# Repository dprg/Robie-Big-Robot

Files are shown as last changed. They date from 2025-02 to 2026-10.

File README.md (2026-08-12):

# Robie-Big-Robot
Files related to Robie, the 7-foot tall DPRG mascot.

# Repo Contents

CAD models are in [mechanical/cad_files](mechanical/cad_files) . At the time of repo creation they contained 
the design files delivered by Ron Grant to Paul Bouchier on 26 Feb 2025.

Arduino files are as delivered by Doug Paradis to Paul Bouchier on March 2 2025. 
Mike Williamson added the Robie_neck_eyes code for the head UNO 7/7/2026.

Raspberry Pi4 files TBD
=======

There are two Arduino source code directories:

1. `Big_robot_pgm1` contains arduino code for the body and arm motors, which are controlled by
the arduino mega in the torso.
2. `Robie_neck_eyes` contains arduino code for the head motors and eye LEDs.

# Raspberry Pi Head Tracking

1. Connect to Robie's AP: `robiewifi`, wifi passwd is inside the body
2. You will get an IP at: `10.42.0.x`
3. ssh into the RPi: `ssh robie@10.42.0.1` # passwd is inside the body
4. Use aliases `miniterm_head` and `miniterm_body` to connect to the arduinos and manually issue commands. `Ctrl-]` to exit
5. Connect a NoMachine client to robie desktop as above
6. launch a terminal session on the desktop
7. In the terminal session:
   - `cd Robie-Big-Robot/src`
   - `source venv/bin/activate`
   - `python face_detector.py`

# Motors

### New Head Pan Motor

A stepper motor to pan the head is now located in the neck of Robie instead of in the torso.

The head motor is a NEMA 11 motor from stepperonline.com, P/N 11HS20-0674S.
[Specs here](https://www.omc-stepperonline.com/nema-11-bipolar-1-8deg-12ncm-17oz-in-0-67a-6-2v-28x28x51mm-4-wires-11hs20-0674s)

There are still 20 command steps for full range using 'L' and 'R' char commands.
There is also a new head center 'C' command.

### New Head Tilt Motor

The head tilt motor is a NEMA 17 motor from stepperonline.com, P/N 17HS19-2004S1.

#### Specs
[Full size image](images/NEMA17-Motor-spec.webp)<br>
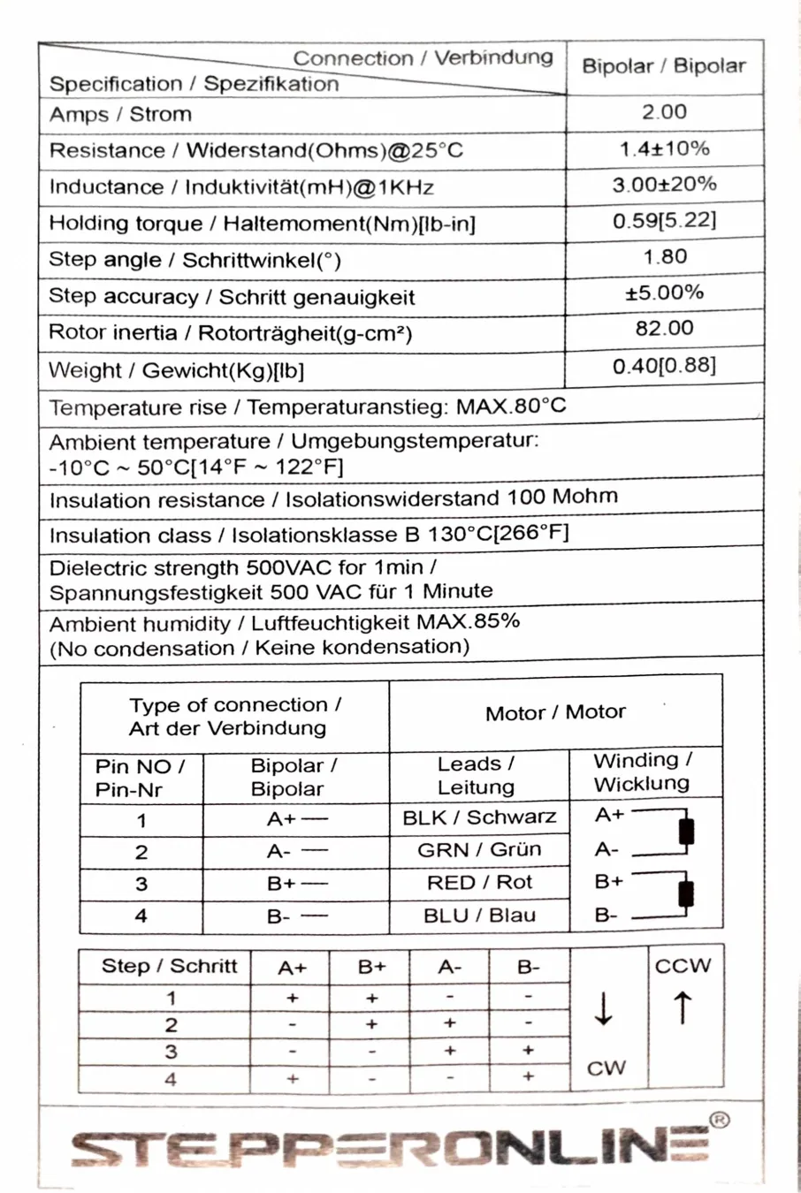
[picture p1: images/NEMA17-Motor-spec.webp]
Tilt motor


It uses a BigTreeTech TMC2209 stepper controller module controlled my the head UNO.
The head movement limit is now detected by current sensing stall technology in the 2209.
[Wiki here](https://global.bttwiki.com/TMC2209.html)

There are 10 command steps for full range using 'U' and 'D' char commands.
There is also a new head center 'C' command.

# System Architecture

Robie is controlled by a Raspberry Pi 4 which sends motion commands to two arduinos:

1. Body Arduino: controls motors in arms
2. Head Arduino: controls head

The Raspberry Pi has a USB camera feed from the eye area, and uses it to recognize faces
and move the head to command the Head Arduino to move the head to track the biggest
(presumably nearest) face in the frame.

The raspberry pi built-in wifi interface is used to connect to wifi networks (e.g. DMS-member).
The raspberry pi has an add-in USB wifi dongle that offers an AP. Login details for the
AP and the Raspberry Pi are on the Robie's back door.

## Shoulder rotate and lift motors

The right shoulder rotate and lift motors are DC motors, with HW limit switches
that interrupt motor power when a limit is hit. The limit state is not
available to FW, but the current position is sensed by a potentiometer
and is available to FW.  The rotate motor rotates the right arm about
the shoulder in the forward direction, and the lift motor lifts the
right arm sideways.  The range of motion available between limits is
180 degrees for both rotate and lift. The lift sensing pot reads 100 -
770 in the ADC at each extreme.  The rotate sensing pot reads 230 -
950 in the ADC at each extreme.  When commanded to take a step move,
the motor is run for 40ms with a PWM speed of 125.  This motor has a
"move to position" function in FW, wherein the FW drives the motor until
the potentiometer achieves a requested feedback value. Note that the
weight of the arm means the arm travels downward further than upward
for a single move request.

## Left wave motor

The left wave motor twists the hand on the forearm. It is a regular servo
with 360 degrees (approx) range of motion, and it moves to the position
requested by the applied PWM.

## Right wave motor

The right wave motor twists the hand on the forearm. It is a continuous-rotation servo
and is stationary for mid-range applied PWM, and rotates continuously at different speeds
based on how far the applied PWM is from mid-range.

# Arduino API

The commands available from the arduino are listed here. They are received on the serial
ports, and can come from a human on a comms terminal or a program driving serial commands.

---

### Legacy Commands

These commands are the API as of early 2025. Commands are single letters and
are executed immediately upon receipt (no CR-LF required). Multiple commands
are buffered and executed in order.

  - L - Pan head left. Responds with L  
  - R - Pan head right. Responds with R
  - U - Tilt head up. Responds with U
  - D - Tilt head down. Responds with D.
  - W - Rotates left wrist twice in each direction. Responds with W.
  - E - Rotates right wrist twice in each direction. Responds with E.
  - 1 - Lift the arm sideways (up/away from body). Responds with: (lift_feedback, rotate_feedback)
  - 2 - Rotate the arm CCW on the shoulder. If the arm is hanging down this results
  in forward and up motion. Similar response as 1 except echoes 2
  - 3 - The opposite of 1. Similar response as 1 except echoes 3
  - 4 - The opposite of 2. Similar response as 1 except echoes 4
  - 5, 6, 6, 7 - Move to fixed poses. Responds with a series of (lift_feedback, rotate_feedback)
  pairs until movement is complete.

**The LRUD commands are now processed in the UNO in its head.
A new C (Center) command centers the head to look slightly down and straight ahead.**

## Electronics, power distribution and wiring

The overall body wiring diagram is in the electrical/EasyEDA project directory.
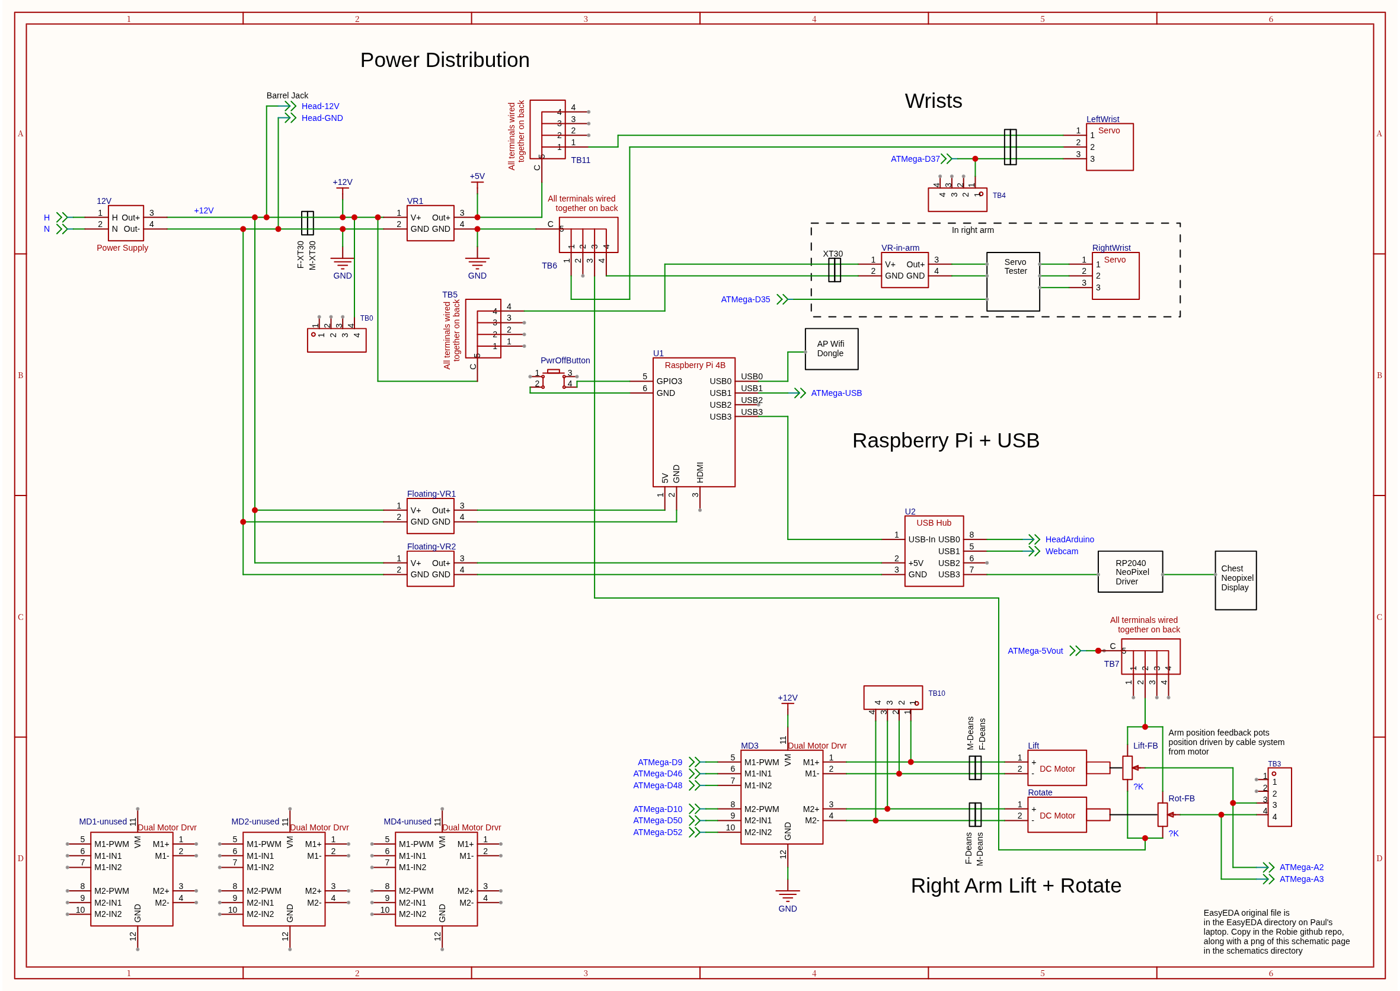
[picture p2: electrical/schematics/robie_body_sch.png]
robie body wiring diagram


### Raspberry Pi4

There is a Pi4 in the torso that processes the images from the head camera and send commands to the Torso MEGA and Head UNO over USB serial cables to cause motion of head and arms. 

### Torso Arduino MEGA controller

The MEGA controls the arms and wrist movements.
The head movement are now controlled by the UNO in its head.

### Head Arduino UNO controller

The UNU now has a DIY shield for the TMC2209 stepper motor modules 
and eyes and 12V connections.
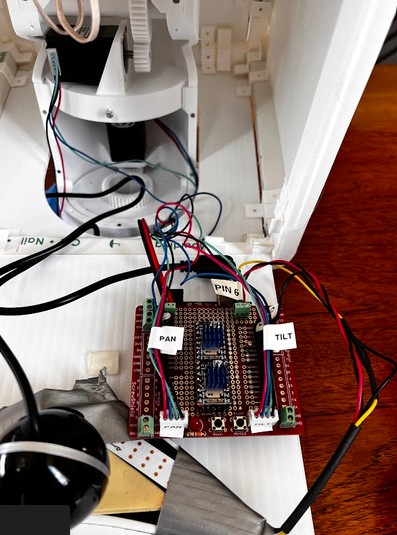
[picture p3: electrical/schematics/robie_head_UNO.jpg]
Robie head and eyes UNO with shield

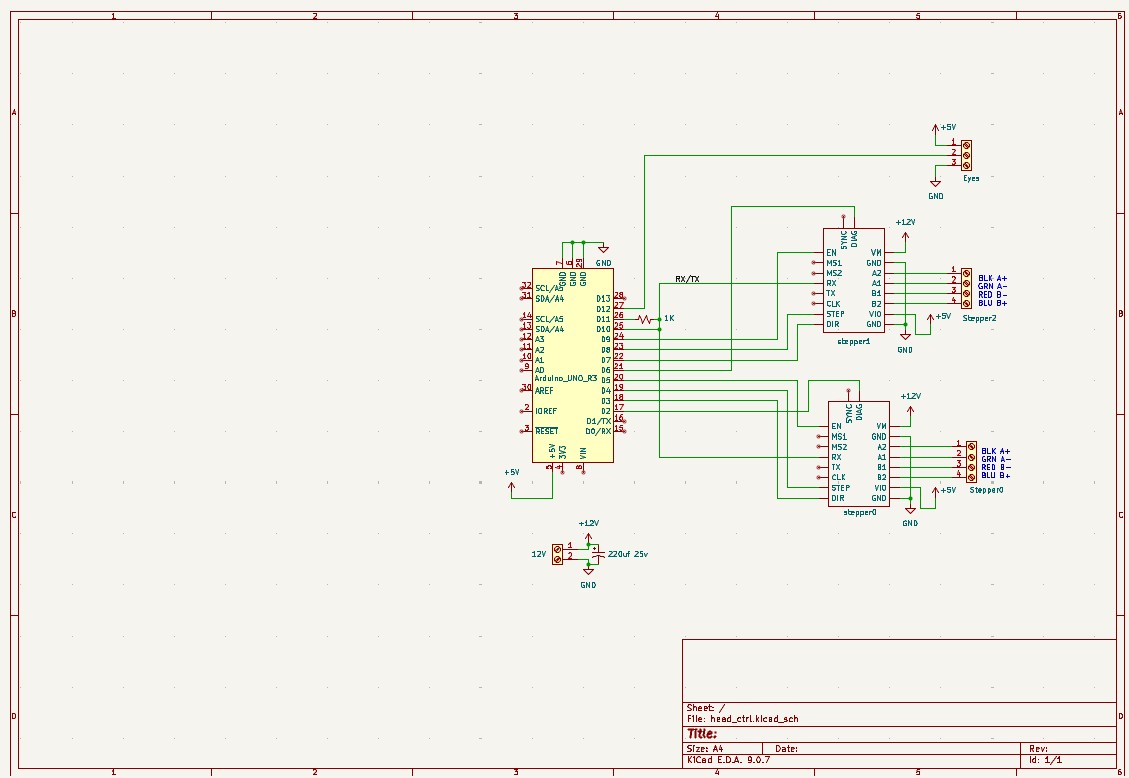
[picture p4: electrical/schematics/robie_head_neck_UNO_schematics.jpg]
Robie head and eyes schematic


# Raspberry Pi SW install instructions

## Install Raspberry Pi OS

- Use rpi-imager to create a bootable SD card with Raspberry Pi OS (Bookworm). Bookworm
is important because, as of July 2026, the mediapipe face recognizer software doesn't
run on the Trixie release. Set the environment to connecto to your local wifi, and create
user account "robie" with a suitable password
- Connect a physical keyboard/mouse/monitor and boot the RPi
- Start the ssh service (it is pre-installed with Raspberry Pi OS):
```bash
sudo systemctl enable ssh
sudo systemctl start ssh
```
- Log into the RPi from a laptop to verify everything is working

## Add USB wifi dongle as access point

Note: you need to be very selective - only a few wifi dongles support modern Linux and Raspberry Pi OS

```bash
sudo nmcli connection add type wifi con-name "USB_Hotspot" ifname wlan1 ssid "robiewifi" mode ap ipv4.method shared
sudo nmcli connection modify "USB_Hotspot" wifi-sec.key-mgmt wpa-psk wifi-sec.psk "YourSecurePassword"
sudo nmcli connection up "USB_Hotspot"
sudo nmcli connection modify "USB_Hotspot" connection.autoconnect yes
sudo nmcli connection modify "USB_Hotspot" connection.permissions ""
```

## Install mediapipe and opencv
You need to set up a virtual environment to install these python packages without compromising
the python system.

```bash
# 1. Install core system prerequisites
sudo apt update && sudo apt install -y python3-venv python3-pip

# 2. Create and activate a clean environment
cd Robie-Big-Robot/src
python -m venv venv
source venv/bin/activate

# 3. Upgrade your package installers inside the environment
pip install --upgrade pip setuptools wheel

# 4. Attempt the installation
pip install pyserial
pip install "opencv-contrib-python<5.0"
pip install mediapipe=0.10.14
```

# Arduino Installation Instructions

Arduino 1.8 is installed on the Raspberry Pi, so you can edit arduino code directly on the
RPi desktop and program the arduino from the RPi without disconnecting anytthing.

When installing this repo to build arduino code on a new machine you'll need to install three
libraries for the head project:

- TMCStepper
- MultiStepperLite
- Adafruit_NeoPixel

# Robie's Wish List

***Things Robie could really use:***

## Mechanical upgrades & fixes desired

- The green visor makes webcam vision difficult. It darkens the scene, and cameras that don't
have automatic white balance will fail because the whole scene looks green, which upsets the
face detection. The desire is to have a wider angle camera with an untinted view of the scene.
How to do this?

## Electrical upgrades & fixes desired

- The connectors for the right shoulder pots should be on keyed wiremount
connectors that don't fall apart all the time
- The flying lead going to D35 which drives the right wrist needs to
get wired to a terminal block, and thence to a 3-wire (at least) unique
connector going up into the arm, replacing the XT30 that currently
supplies power to the right wrist.
- An elbow (with a BLDC motor) would give it much more expressiveness.

### Software upgrades & fixes desired

- Provide a parser better suited to computer control. The current
parser is good for human interaction, but has weaknesses for
API interaction (irregular feedback) and is not suited to async operation.
It would be desirable for it to use a different serial port, and be a
whole different parser that uses json to pass commands & status, so
as to retain the debug output and human-interactive aspects of the
current parser on the arduino serial port.

## Media

Robie Resuscitation 2025
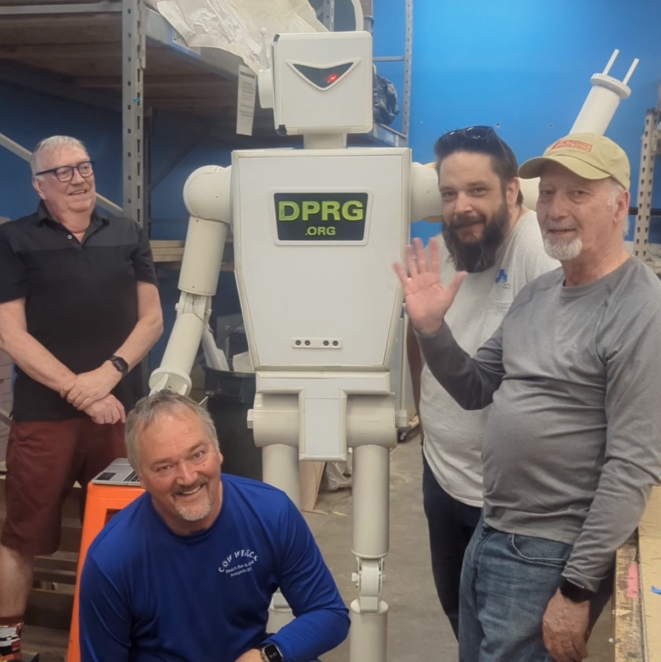
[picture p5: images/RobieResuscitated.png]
Robie Resuscitated


Robie at iMake Ft Worth (2017)
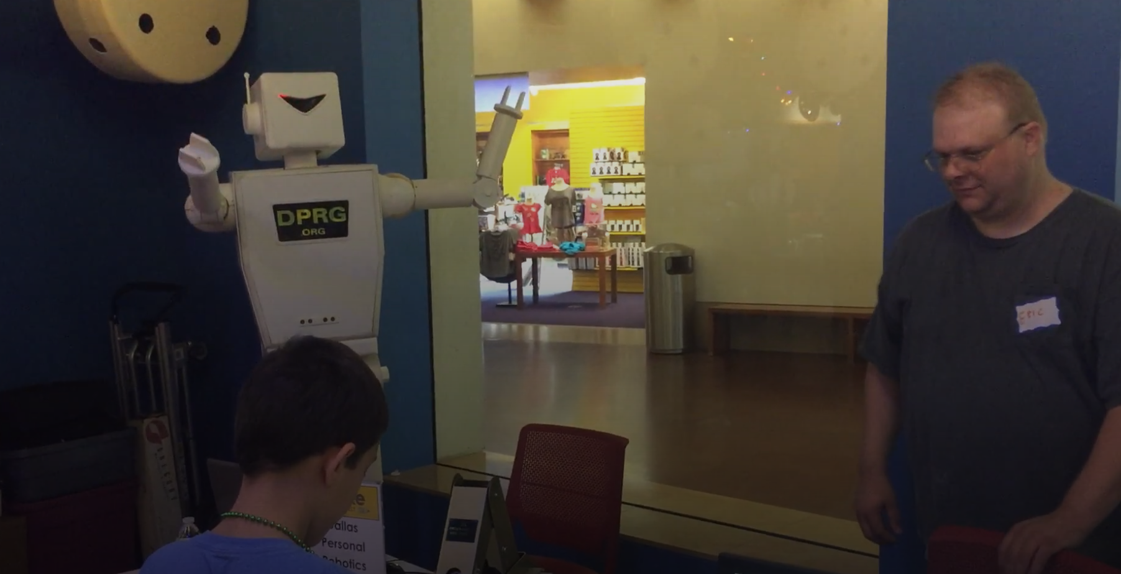
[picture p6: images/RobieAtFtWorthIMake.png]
Robie at iMake Ft Worth (2017)


Robie with Doug
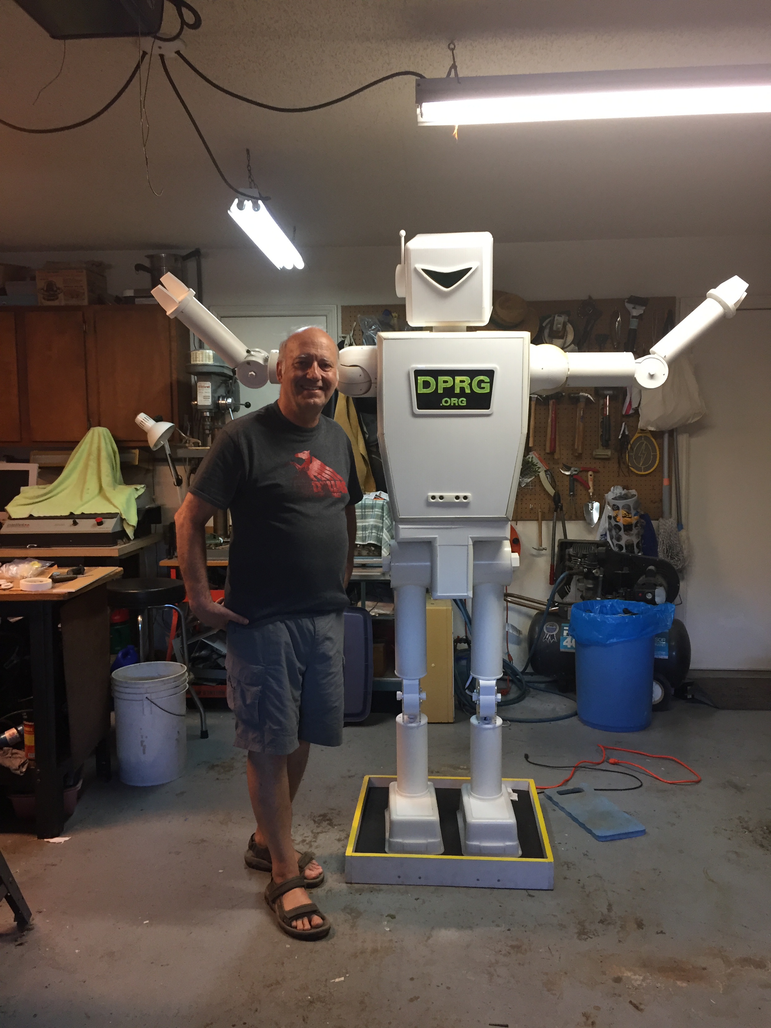
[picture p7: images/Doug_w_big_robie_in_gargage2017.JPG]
Robie with Doug


### Videos
[Video: Resuscitated Robie moving](https://youtu.be/EISYc3Z7FQA)

[Video: Early Robie at a DPRG show](https://youtu.be/n2Y_eyLx5xM)

## Changelog

Mike W 3/21/2025
- Added opencv code to detect faces which will control the head to point to it and maybe even wave when centered on face
  - start code: cd to opencv in terminal run py -f facedet_test.py

Mark R 3/26/2025
- Added support for Linux, as well as some error catching stuff

It is based on the instructions from this page:
https://thepythoncode.com/article/detect-faces-opencv-python 

Paul B 4/1/2025
- Removed duplicate arduino directory Big_robot_pgm2. Added image to README.md

Mike W 7/7/2026
- Added code for the UNO in Robie's head. It now controlls the pan and tilt steppers as well as the eyes

Mark R 7/21/26
- Update the file structure to hopefully make it a little clearer

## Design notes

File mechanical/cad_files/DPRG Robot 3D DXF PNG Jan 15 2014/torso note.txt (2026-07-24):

torso width 16.0" at shoulders cut off in PNG file

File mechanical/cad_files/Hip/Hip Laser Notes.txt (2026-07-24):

RG Laser (40 Watt CO2)

Styrene .125" Thick ($2.50/sqft e-street)
p160  f100 (10.0 ipm)

Acrylic 1/4" Thick
p160  f60

Styrofoam (monitor - fire hazard)
Use Higher Pressure Assist Air (Med Pump)

p150 f150  - some edge roughness (another setting did better -- maybe p160 f100?)
used this setting to make 7 knee plates

Foam Stack + 1/8 Plex 2.020

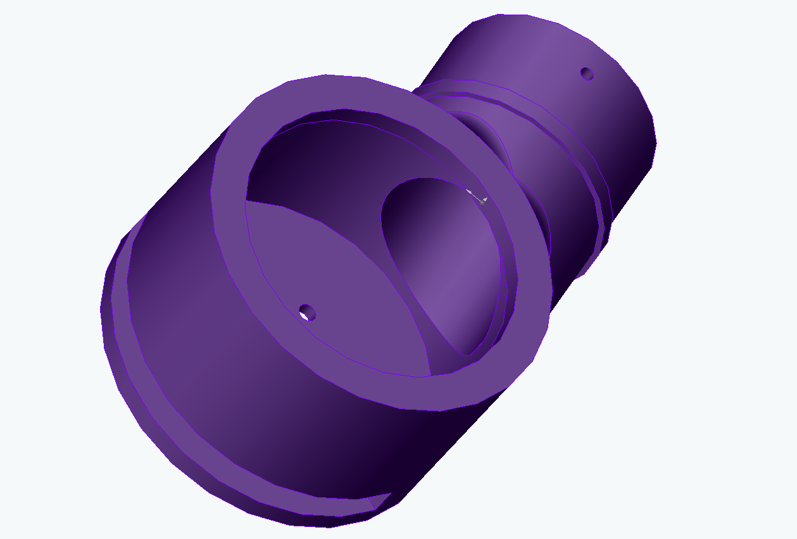
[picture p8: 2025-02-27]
mechanical/cad_files/Elbow/elbowlower2.tif

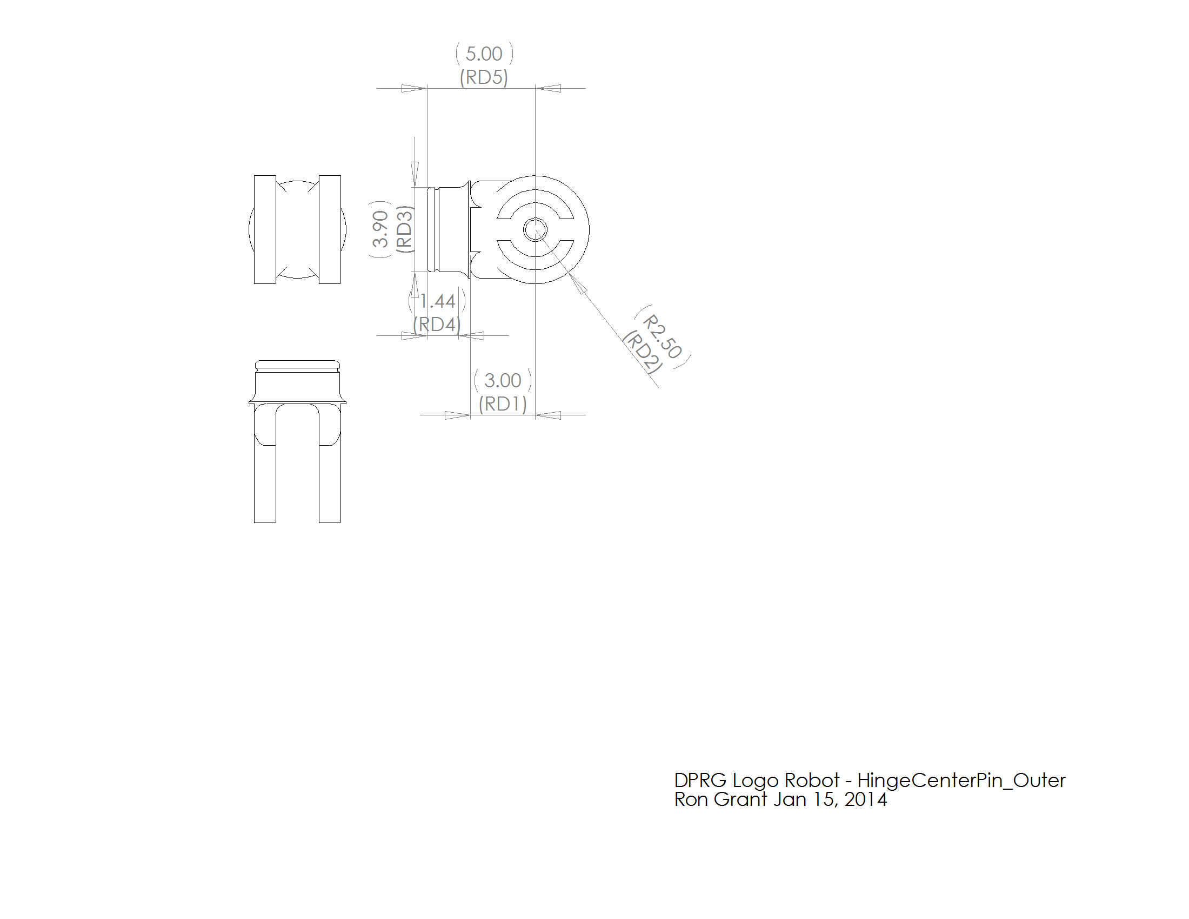
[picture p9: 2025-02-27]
mechanical/cad_files/DPRG Robot 3D DXF PNG Jan 15 2014/hingecenterpin_outer.png

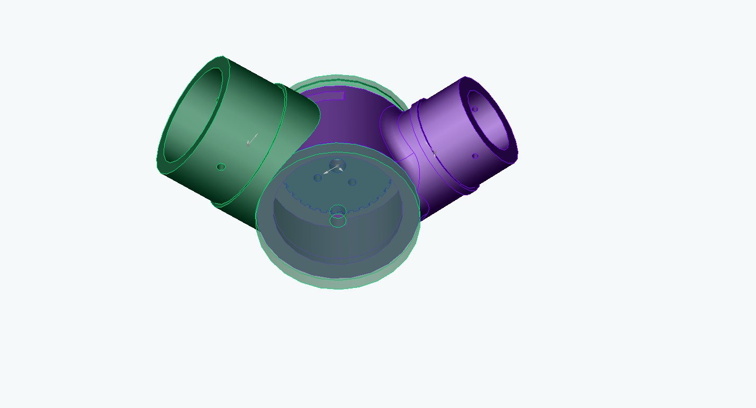
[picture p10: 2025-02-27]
mechanical/cad_files/Elbow/JpegElbow3D_Feb21_2014/elbow4.jpg

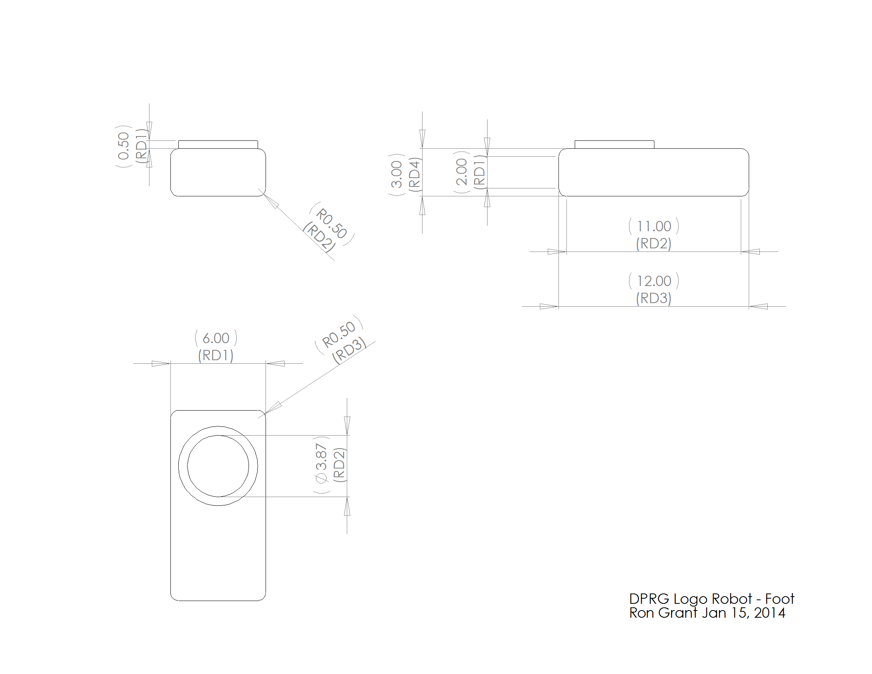
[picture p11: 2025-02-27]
mechanical/cad_files/DPRG Robot 3D DXF PNG Jan 15 2014/foot.png

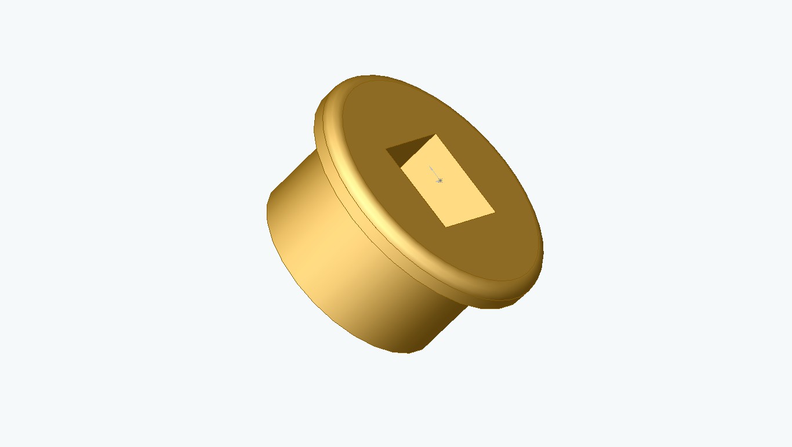
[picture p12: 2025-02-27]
mechanical/cad_files/DPRG Robot 3D DXF PNG Jan 15 2014/hingejoint_inner2part_pipeboss.jpg

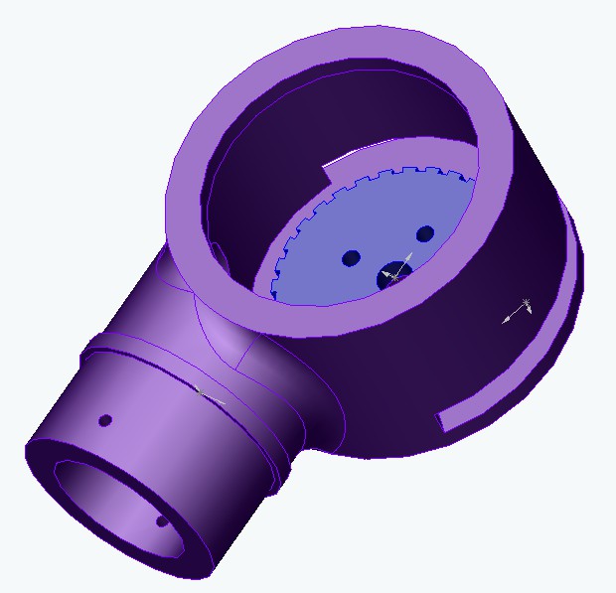
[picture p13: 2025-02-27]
mechanical/cad_files/Elbow/JpegElbow3D_Feb21_2014/elbow3.jpg

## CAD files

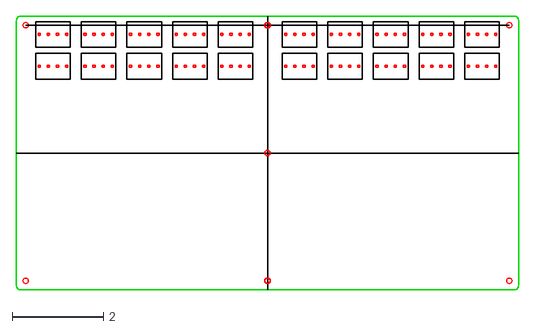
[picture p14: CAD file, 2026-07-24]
mechanical/cad_files/Electronics/MainBoard_BLOCKS.dxf
11.0 x 6.00

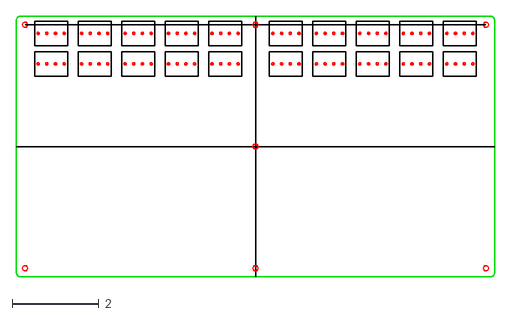
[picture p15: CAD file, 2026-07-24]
mechanical/cad_files/Electronics/MainBoard.dxf
11.0 x 6.00

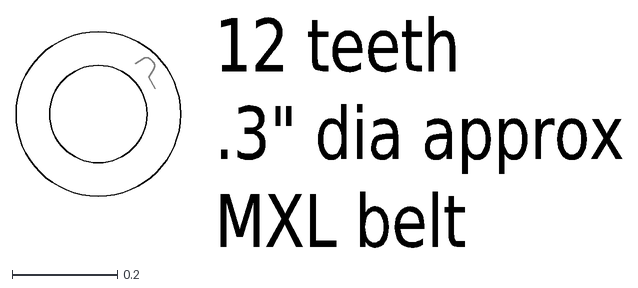
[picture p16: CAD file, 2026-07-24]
mechanical/cad_files/Elbow/MXL 080 Timing Belt Gears/a_6a15-012mxl02_incomplete.dxf
12 teeth
.3" dia approx
MXL belt

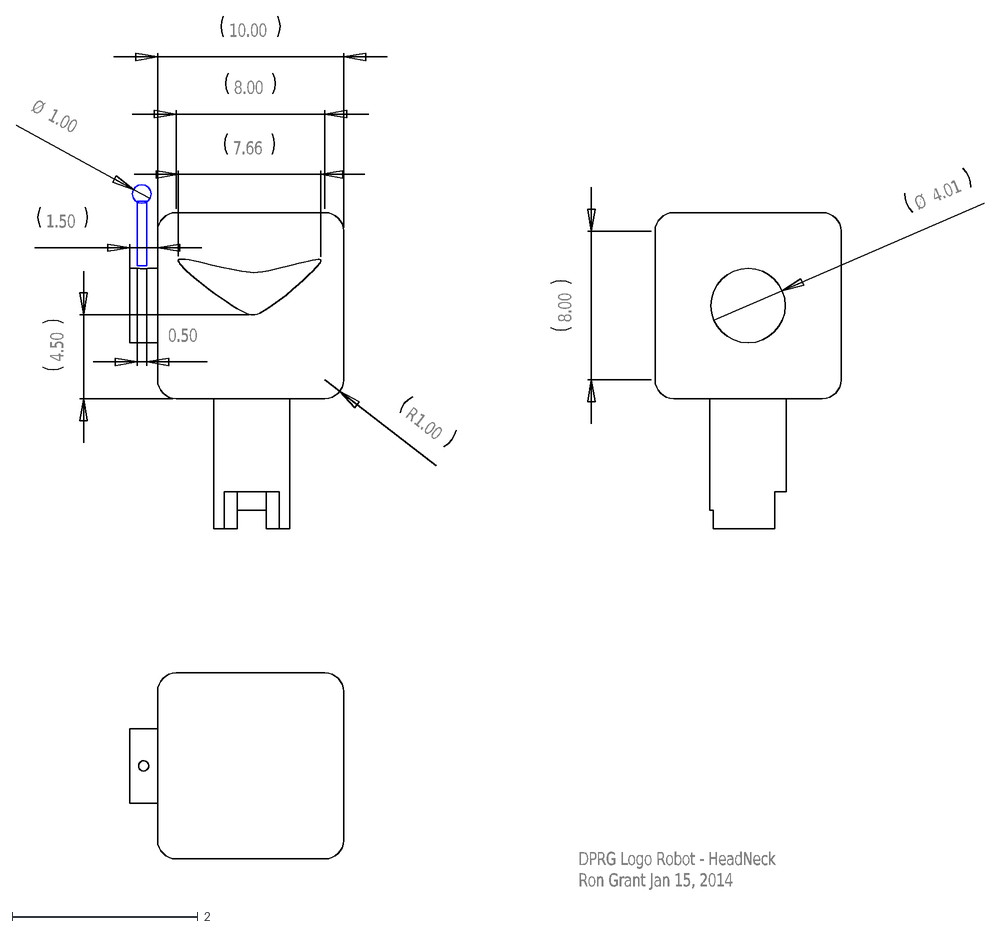
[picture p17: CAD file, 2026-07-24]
mechanical/cad_files/DPRG Robot 3D DXF PNG Jan 15 2014/HeadNeck.dxf
0.50
Ø
1.00
8.00
10.00
7.66
4.50
R
1.50
DPRG Logo Robot - HeadNeck Ron Grant Jan 15, 2014
4.01

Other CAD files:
mechanical/cad_files/Shoulder Will Kuhnle/Shoulder.SLDASM
mechanical/cad_files/Elbow/Elbow.SLDASM
mechanical/cad_files/Hand/Hand.SLDASM
mechanical/cad_files/Knee REPAIR 2025/YokePlate25_175Thick_Repair2024_Main.SLDPRT
mechanical/cad_files/Hand/Linkage.SLDASM
mechanical/cad_files/Platform/Platform.SLDASM
mechanical/cad_files/Knee/YokeOuter.SLDASM
mechanical/cad_files/Pelvis/PelvisThreeQuarterRound.SLDASM
mechanical/cad_files/Rounded Corners/CornerJoin.SLDASM
mechanical/cad_files/Elbow/ElbowPlates2/ElbowDriveModule.SLDASM
mechanical/cad_files/Rounded Corners/Corner..SLDASM
mechanical/cad_files/Knee/YokePlateShroudFull.SLDPRT
mechanical/cad_files/Elbow/ElbowPlates2/Elbow2.SLDASM
mechanical/cad_files/Pelvis/Pelvis.SLDASM
mechanical/cad_files/DPRG Robot 3D DXF PNG Jan 15 2014/DPRG Logo Robot 2.dxf
mechanical/cad_files/DPRG Robot 3D DXF PNG Jan 15 2014/Foot.DXF
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

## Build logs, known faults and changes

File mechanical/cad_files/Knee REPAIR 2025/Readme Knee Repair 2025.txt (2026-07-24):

For the repaired knee inner yoke, 2025 Feb

The original "inner" knee has 3 pieces of styro foam.

I changed this up a bit including FoamRep component to be paired with
.175" thick piece printed on printer that would not fit entire part
(black component of the 2025 repair), but then needed to add another part,
the "Cover" to total the thickness needed to fit within the joint yoke.

And then if not mistaken, I printed a 4th part "shim" 0.13" thick to correct
for a measurment error...  What a mess..., but was out of time to get repaired kneee delivered for Feb Meeting... 

The replacement inner yoke if that is correct term  is a stack of three components.

The 5/16" bolts are needed to keep join locked in vertical position...

Stack if I have it right is:

YokePlate25_FoamRep_Feb2025.STL              PLA thickest piece with wire channel
YokePlate25_175Thick_Repair2024_Main.STL     black nylon carbon fiber with separate piece
YokePlate25_Cover_Feb2025.STL

Finally due to error cover extruded 0.13" to compensate for error, save time printing 
thin plate

YokePlate25_Cover_Feb2025_SHIM013.STL

Really entire inner knee could be printed in 2 parts, or a single part if wire channel not needed.

Hopefully this makes some sense if anyone ever reads this!
Ron Grant   Feb 26, 2025

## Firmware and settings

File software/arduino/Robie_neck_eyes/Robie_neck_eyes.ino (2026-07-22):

/***********************************
// Robie_neck_eyes Arduino sketch
// Stored on GitHub 
// https://github.com/dprg/Robie-Big-Robot
//
// Two steppers, head PAN and TILT
// 27 Eye LEDs (neo-pixel type)
//
// Head serial character commands:
// C - Centers the head looking slightly down
// L - Look left
// R - Look right
// U - Look up
// D - look down
// Pan full range is 20 Rs or Ls
// Tilt full range 10 Us or Ds
// Multiple commnads can be sent per line string
//
// Eye default motion is a RED dot cycling left and right
// But while responding to LRUD the eyes are blue dots in the
// direction of movement
//
// The serial interface to the 2 stepper modules is a 
// single bi-dir multi-drop wire
// Each stepper module has its own address
//
// 7/7/2026 Mike Williamson
***********************************/

#include <TMCStepper.h>
#include <SoftwareSerial.h>
#include "AccelStepper.h"
#include <Adafruit_NeoPixel.h>

#define USB_SERIAL_BAUD 115200L
#define STEPPER_SERIAL_BAUD 115200L

#define stepper0_enaPin   5
#define stepper0_stepPin  4
#define stepper0_dirPin   3
#define stepper0_diagPin  2

#define stepper1_enaPin   9
#define stepper1_stepPin  8
#define stepper1_dirPin   7
#define stepper1_diagPin  6

#define SW_RX            10 // SoftwareSerial receive pin
#define SW_TX            11 // SoftwareSerial transmit pin

#define eyesPin          12
#define diagLedPin			 13

AccelStepper stepper0(AccelStepper::DRIVER, stepper0_stepPin, stepper0_dirPin); //initialize tilt stepper
AccelStepper stepper1(AccelStepper::DRIVER, stepper1_stepPin, stepper1_dirPin); //initialize pan stepper

SoftwareSerial swSerial(SW_RX, SW_TX); // For stepper config

#define SERIAL_PORT Serial3 // TMC2208/TMC2224 HardwareSerial port
#define DRIVER0_ADDRESS 0b00 // MS2,MS1  = 00
#define DRIVER1_ADDRESS 0b01 // MS2,MS1  = 01


#define R_SENSE 0.11f // Match to your driver
                      // SilentStepStick series use 0.11

// TILT driver0 and stepper0 controls the head tilt
TMC2209Stepper driver0(&swSerial, R_SENSE, DRIVER0_ADDRESS);  
#define STEPPER0_STALLVALUE  15 // [0..255]
#define STEPPER0_I 			     1800 // ma
#define STEPPER0_MICROSTEPS  2 // 1/N micro stepping 2,4,8,16,32

// PAN driver1 and stepper1 controls the head pan
TMC2209Stepper driver1(&swSerial, R_SENSE, DRIVER1_ADDRESS);  
#define STEPPER1_STALLVALUE  0 // [0..255]
#define STEPPER1_I 			     800 // ma
#define STEPPER1_MICROSTEPS  2 // 1/N micro stepping 2,4,8,16,32

// stepper motion configuration - does not configure 2290 module
// TILT Up Down
#define STEPPER0_TIME_FS	 1.0 // full scale travel time (sec)
#define STEPPER0_NCMDS_FS    10 // Number of UD commands to travel full scale
#define STEPPER0_STEPS_FS    50 //34 // full scale range steps not micro steps
#define STEPPER0_STEPS       (STEPPER0_MICROSTEPS*STEPPER0_STEPS_FS) // micro steps
#define STEPPER0_MAXSPEED    STEPPER0_STEPS/STEPPER0_TIME_FS // steps per sec
#define STEPPER0_TIME2MAX    1.0 // time to accelerate to max speed (sec)
#define STEPPER0_ACCELERATION STEPPER0_MAXSPEED/STEPPER0_TIME2MAX // acceleration (steps/sec^2)
#define STEPPER0_UDSTEPS	 (STEPPER0_STEPS/STEPPER0_NCMDS_FS) // UD commaand steps
#define STEPPER0_UDIR        1 // tilt up stepper direction
#define STEPPER0_DDIR        0 // tilt down stepper direction
// PAN Right Left
#define STEPPER1_TIME_FS	 2.0 // full scale travel time (sec)
#define STEPPER1_NCMDS_FS    20 // Number of RL commands to travel full scale
#define STEPPER1_STEPS_FS    124 // full scale range steps not micro steps
#define STEPPER1_STEPS       (STEPPER1_MICROSTEPS*STEPPER1_STEPS_FS) // micro steps
#define STEPPER1_MAXSPEED    STEPPER1_STEPS/STEPPER1_TIME_FS // steps per sec
#define STEPPER1_TIME2MAX    1.0 // time to accelerate to max speed (sec)
#define STEPPER1_ACCELERATION STEPPER1_MAXSPEED/STEPPER1_TIME2MAX // acceleration (steps/sec^2)
#define STEPPER1_LRSTEPS		 (STEPPER1_STEPS/STEPPER1_NCMDS_FS) // RL command steps
#define STEPPER1_LDIR        1 // pan left stepper direction
#define STEPPER1_RDIR        0 // pan right stepper direction

enum headCmds {
	Idle,
	Center,
	Left,
	Right,
	Up,
	Down
};

headCmds headCmd = Idle;
headCmds headCmdLast = Idle;

bool tiltStallDet = false;
bool panStallDet  = false;
int headCmdStallCnt = 0;

// States for head centering
enum centerStates {
	Wait,
	TiltLimitA,
	TiltLimitB,
	TiltCenterA,
	TiltCenterB,
	PanLimitA,
	PanLimitB,
	PanCenterA,
	PanCenterB,
	Done
};

bool panRightBusy = false;
bool panLeftBusy  = false;
bool tiltUpBusy   = false;
bool tiltDownBusy = false;


//EYES
// How many NeoPixels are attached to the Arduino?
#define NUMPIXELS 27 // Num leds in Robies eye plate
#define DELAYVAL 50 // Time (in milliseconds) to pause between pixels

// When setting up the NeoPixel library, we tell it how many pixels,
// and which pin to use to send signals. Note that for older NeoPixel
// strips you might need to change the third parameter -- see the
// strandtest example for more information on possible values.
Adafruit_NeoPixel pixels(NUMPIXELS, eyesPin, NEO_RGB + NEO_KHZ800);

/////////////////////////////////////////////////////////////////////////
// SETUP functions

void setupDrivers() {
  //SERIAL_PORT.begin(STEPPER_SERIAL_BAUD);
  swSerial.begin(STEPPER_SERIAL_BAUD);

	// Stepper driver 0
  driver0.begin();

  driver0.toff(4);
  driver0.blank_time(24);
  driver0.TCOOLTHRS(0xFFFFF); // 20bit max
  driver0.semin(5);
  driver0.semax(2);
  driver0.sedn(0b01);

  driver0.rms_current(STEPPER0_I);        // Set motor RMS current
  driver0.microsteps(STEPPER0_MICROSTEPS);          // Set microsteps to 1/16th
  driver0.SGTHRS(STEPPER0_STALLVALUE);

	// Stepper driver 1
  driver1.begin();

  driver1.toff(4);
  driver1.blank_time(24);
  driver1.TCOOLTHRS(0xFFFFF); // 20bit max
  driver1.semin(5);
  driver1.semax(2);
  driver1.sedn(0b01);

  driver1.rms_current(STEPPER1_I);        // Set motor RMS current
  driver1.microsteps(STEPPER1_MICROSTEPS);          // Set microsteps to 1/16th
  driver1.SGTHRS(STEPPER1_STALLVALUE);

}

void setupSteppers() {
	//enable both motors and set directions
	pinMode(stepper0_enaPin, OUTPUT);
	pinMode(stepper0_dirPin, OUTPUT);
	pinMode(stepper0_diagPin, INPUT);
	digitalWrite(stepper0_enaPin, LOW);
	digitalWrite(stepper0_dirPin, LOW);

	pinMode(stepper1_enaPin, OUTPUT);
	pinMode(stepper1_dirPin, OUTPUT);
	pinMode(stepper1_diagPin, INPUT);
	digitalWrite(stepper1_enaPin, LOW);
	digitalWrite(stepper1_dirPin, LOW);

	stepper0.setMaxSpeed(STEPPER0_MAXSPEED);
	stepper0.setAcceleration(STEPPER0_ACCELERATION);
	stepper1.setMaxSpeed(STEPPER1_MAXSPEED);
	stepper1.setAcceleration(STEPPER1_ACCELERATION);
}

void setupEyes(){
  pixels.begin(); // INITIALIZE NeoPixel strip object (REQUIRED)
  pixels.clear(); // Set all pixel colors to 'off'
}

//////////////////////////////////////////////////////////////////////////////
// LOOP tasks

// Process serial port for commands
// Single char comads are:
// C Center head pan and tilt (uses stops to calibrate movement)
// R L Pan head Right and left 1 movement
// U D Tilt head Up and Down 1 movement
void	commandsTask(uint32_t now_ms) {
	if(headCmd != Idle) {
		return;
	}

	if(!Serial.available()) return;
	// read serial port character
	char c = Serial.read();
  if ((c >= 97) && (c <= 122))  // char is lower case
    c -= 32;                    // change to upper case
	if (c=='C') {
		// Serial.println("Center head position");
		headCmd = Center;
		headCmdLast = headCmd;
	}
	else if (c=='R') {
		// Serial.println("Pan head RIGHT");
		headCmd = Right;
		headCmdLast = headCmd;
	}
	else if (c=='L') {
		// Serial.println("Pan head LEFT");
		headCmd = Left;
		headCmdLast = headCmd;
	}
	else if (c=='U') {
		// Serial.println("Tilt head UP");
		headCmd = Up;
		headCmdLast = headCmd;
	}
	else if (c=='D') {
		// Serial.println("Tilt head DOWN");
		headCmd = Down;
		headCmdLast = headCmd;
	}
}

void diagTask(uint32_t now_ms) {
  static uint32_t last_time=0;
	static int diag0 = 0;
	static int diag1 = 0;
	static bool lastDiag0Pin = false;
	static bool lastDiag1Pin = false;

	bool currentDiag0Pin = digitalRead(stepper0_diagPin);
	bool currentDiag1Pin = digitalRead(stepper1_diagPin);

	diag0 += ((!lastDiag0Pin)&&currentDiag0Pin)?1:0;
	diag1 += ((!lastDiag1Pin)&&currentDiag1Pin)?1:0;
	
	if (headCmd != headCmdLast) {
		headCmdStallCnt = 0;
	}
	else if (currentDiag0Pin) {
		if (headCmdLast==Up)   headCmd = Idle;
		if (headCmdLast==Down) headCmd = Idle;
	}
	else if (currentDiag1Pin) {
		if (headCmdLast==Right) headCmd = Idle;
		if (headCmdLast==Left)  headCmd = Idle;
	}

	lastDiag0Pin = currentDiag0Pin;
	lastDiag1Pin = currentDiag1Pin;

  if((now_ms-last_time) > 100) { //run every 0.1s
    last_time = now_ms;

		digitalWrite(diagLedPin, (diag0>0|diag1>0));
    Serial.print(diag1); Serial.print(" "); Serial.print(diag0);

		if(diag0>0) tiltStallDet = true;
		if(diag1>0) panStallDet  = true;

		diag0 = 0;
		diag1 = 0;

		// NOTE: reading driver consumes a lot of cycles and slows the stepper motion and eyes
		// uint16_t sg = driver0.SG_RESULT();
    // Serial.print(" ");
    // Serial.print(sg, DEC);

		Serial.println();
	}
}

void steppersTask(uint32_t now_us){

	stepper0.run();
	stepper1.run();

	bool stepper0_finished = stepper0.distanceToGo() == 0;
	bool stepper1_finished = stepper1.distanceToGo() == 0;

	//turn off busy flags when command finishes
	if (stepper1_finished) {
		if (panLeftBusy)  panLeftBusy  = false;
		if (panRightBusy) panRightBusy = false;
	}
	if (stepper0_finished) {
		if (tiltUpBusy)   tiltUpBusy   = false;
		if (tiltDownBusy) tiltDownBusy = false;
	}

	if (headCmd == Idle) return;

	
	if (stepper1_finished) {
		if (headCmd == Left) {
			stepper1.move(STEPPER1_LRSTEPS);
			headCmd = Idle;
			panLeftBusy = true;
		}
		else if (headCmd == Right) {
			stepper1.move(-STEPPER1_LRSTEPS);
			headCmd = Idle;
			panRightBusy = true;
		}	
	}

	if (stepper0_finished) {
		if (headCmd == Up) {
			stepper0.move(STEPPER0_UDSTEPS);
			headCmd = Idle;
			tiltUpBusy = true;
		}
		else if (headCmd == Down) {
			stepper0.move(-STEPPER0_UDSTEPS);
			headCmd = Idle;
			tiltDownBusy = true;
		}
	}

	// Head centering command is a sequence of movements
	static centerStates centerState = Wait;

	if (headCmd == Center) {
		if(centerState==Wait) {
			centerState  = TiltLimitA;
			tiltStallDet = false;
			panStallDet  = false;
		}
		else if(centerState==TiltLimitA) {
			// Move head Up 
			if(stepper0_finished) {
				stepper0.move(STEPPER0_UDSTEPS*STEPPER0_NCMDS_FS);
				centerState = TiltLimitB;
			}
		}
		else if(centerState==TiltLimitB) {
			// keep moving up until stall or stepper finished movement
			if(tiltStallDet || stepper0_finished) {
				tiltStallDet = false;
				stepper0.stop();
				centerState = TiltCenterA;
			}
		}
		else if(centerState==TiltCenterA) {
			// Move Down to center position
			if(stepper0_finished) {
				stepper0.move(-STEPPER0_UDSTEPS*STEPPER0_NCMDS_FS*0.75);
				centerState = TiltCenterB;
			}
		}
		else if(centerState==TiltCenterB) {
			if(stepper0_finished) {
				centerState = PanLimitA;
			}
		}
		else if(centerState==PanLimitA) {
			// Move head Left 
			if(stepper1_finished) {
				stepper1.move(STEPPER1_LRSTEPS*STEPPER1_NCMDS_FS);
				centerState = PanLimitB;
			}
		}
		else if(centerState==PanLimitB) {
			// keep moving left until stall or stepper finished movement
			if(panStallDet || stepper1_finished) {
				panStallDet = false;
				stepper0.stop();
				stepper1.stop();
				centerState = PanCenterA;
			}
		}
		else if(centerState==PanCenterA) {
			// Move Right to center position
			if(stepper1_finished) {
				stepper1.move(-STEPPER1_LRSTEPS*STEPPER1_NCMDS_FS*0.5);
				centerState = PanCenterB;
			}
		}
		else if(centerState==PanCenterB) {
			if(stepper1_finished) {
				centerState = Done;
			}
		}
		else if(centerState==Done) {
			centerState = Wait;
			headCmd = Idle;
		}
	}
}

void eyesTask(uint32_t now_ms) {
static int i = 0;
static bool dir = true;
static uint32_t last_ms = 0;

	if((now_ms-last_ms) < DELAYVAL) return;

	last_ms = now_ms;
	pixels.clear(); // Set all pixel colors to 'off'
	// The first NeoPixel in a strand is #0, second is 1, all the way up
	// to the count of pixels minus one.
	// for(int i=0; i<NUMPIXELS; i++) { // For each pixel...

	if(panLeftBusy) {
		pixels.setPixelColor(7, pixels.Color(0, 0, 200));
		pixels.show();   // Send the updated pixel colors to the hardware.
	}
	else if(panRightBusy) {
		pixels.setPixelColor(20, pixels.Color(0, 0, 200));
		pixels.show();   // Send the updated pixel colors to the hardware.
	}
	else if(tiltUpBusy) {
		pixels.setPixelColor(0, pixels.Color(0, 0, 200));
		pixels.setPixelColor(26, pixels.Color(0, 0, 200));
		pixels.show();   // Send the updated pixel colors to the hardware.
	}
	else if(tiltDownBusy) {
		pixels.setPixelColor(12, pixels.Color(0, 0, 200));
		pixels.setPixelColor(13, pixels.Color(0, 0, 200));
		pixels.setPixelColor(14, pixels.Color(0, 0, 200));
		pixels.show();   // Send the updated pixel colors to the hardware.
	}
	else {

		// pixels.Color() takes RGB values, from 0,0,0 up to 255,255,255
		// Here we're using a moderately bright red color:
		pixels.setPixelColor(i, pixels.Color(150, 0, 0));
		pixels.show();   // Send the updated pixel colors to the hardware.

		if(dir) {
			i++;
			if(i==NUMPIXELS) {
				dir = false;
				i--;
			}
		} else {
			i--;
			if(i==-1) {
				dir = true;
				i++;
			}
		}
	}
}

////////////////////////////////////////////////////////////////////////////////////
// setup and loop executive code

void setup() {
  Serial.begin(USB_SERIAL_BAUD);         // Init serial port and set baudrate
  while(!Serial);               // Wait for serial port to connect
  Serial.print("\nStart...");

	setupDrivers();

  int ver0 = driver0.version();
  int ver1 = driver1.version();
  Serial.print("Driver version for stepper modules 0, 1 : "); Serial.print(ver0,DEC);
  Serial.print(", "); Serial.println(ver1,DEC);

	setupSteppers();

	setupEyes();
}

void loop() {
  uint32_t now_ms = millis();
	uint32_t now_us = micros();

	commandsTask(now_ms);

    steppersTask(now_us);

	diagTask(now_ms);

	eyesTask(now_ms);

}

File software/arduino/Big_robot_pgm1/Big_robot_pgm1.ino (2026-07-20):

/* pan/tilt demostration
 * ---------------------
 * Head moves from limit swith to limit switch for both
 * Pan / tilt motors.
 *
 * Pan is driven by a unipolar 5 wire stepper motor
 * using a ULN2003 motor driver board.
 * Tilt is driven by a DC gearhead motor using
 * an L298 motor driver board.
 *
 * Doug Paradis copyright 2014
 *
 */

#include "Big_robot_pgm1.h"
#include <Stream.h>
#include <Servo.h>

// Pin definitions
const int LED = 13;
const int BUTTON = 12;
const int POT_LIFT = A2; // Pot 1
const int POT_ROT = A3;  // Pot 2

// Serial setup stuff
const int bufLen = 36;    // length of inputString buffer
char inputString[bufLen]; // a string (buffer) to hold incoming data
unsigned long baudRate = 115200;      // baud rate

// servo objects
Servo waveServo; // create servo object to control left wrist servo
Servo waveServo_right; // create servo object to control left wrist servo
                 // a maximum of eight servo objects can be created

// define motors
motor tiltMtr;
motor panMtr;
motor rightShoulderLiftMtr;
motor rightShoulderRotMtr;
motor *ptrTiltMtr = &tiltMtr;
motor *ptrPanMtr = &panMtr;
motor *ptrRightShoulderLiftMtr = &rightShoulderLiftMtr;
motor *ptrRightShoulderRotMtr = &rightShoulderRotMtr;

// define delays
int dcMtrTimeOn = 40;

void setup()
{
  initialize(); // Assumes initialize() sets up pins, serial, servos, motor structs etc.

  // Initialize ALL motor states
  if (ptrTiltMtr) ptrTiltMtr->state = MOTOR_IDLE;
  if (ptrPanMtr) ptrPanMtr->state = MOTOR_IDLE;
  if (ptrRightShoulderLiftMtr) ptrRightShoulderLiftMtr->state = MOTOR_IDLE;
  if (ptrRightShoulderRotMtr) ptrRightShoulderRotMtr->state = MOTOR_IDLE;

  // Initialize Pose state
  isMovingToPose = false;

  // Initialize Wave states
  waveLeftState = WAVE_IDLE;
  waveRightState = WAVE_IDLE;
}

void loop()
{
  // if button pushed, stop all motors
  // note: ESTOP should be when button goes high - fix when estop button added
  //       Also ESTOP should be power not microcontrolle
  // if (digitalRead(BUTTON) == LOW) {
  // ptrTiltMtr->dirChgFlg = ESTOP;
  // ptrPanMtr->dirChgFlg = ESTOP;
  //   digitalWrite(LED, HIGH);
  //}

  // --- Update ALL State Machines ---
  updateDcMotors();       // Handles Tilt, Shoulder motors after startDcMotorStep
  updateStepperMotor();   // Handles Pan motor after startStepperStep
  updateMoveToPose();     // Handles coordinated shoulder movement
  updateWaveLeft();       // Handles left servo wave
  updateWaveRight();      // Handles right servo wave

  // --- Check for Input ---
  int cmdLen = 0;
  cmdLen = readCmdLine(); // Check if a new command has arrived
  if (cmdLen > 0) {
    // A new command arrived. Check if it should be ignored or if it interrupts moveToPose.
    bool ignoreCmd = false;
    char cmdChar = toupper(inputString[0]); // Use uppercase for checks

    // --- Check for Busy States / Ignore Logic ---
    switch(cmdChar) {
        case 'W':
            if (waveLeftState != WAVE_IDLE) { ignoreCmd = true; Serial.println("Ignoring 'W': Left wave busy."); }
            break;
        case 'E':
            if (waveRightState != WAVE_IDLE) { ignoreCmd = true; Serial.println("Ignoring 'E': Right wave busy."); }
            break;
        case 'L':
        case 'R':
            if (ptrPanMtr && ptrPanMtr->state != MOTOR_IDLE) { ignoreCmd = true; Serial.println("Ignoring 'L'/'R': Pan motor busy."); }
            break;
        case 'U':
        case 'D':
            if (ptrTiltMtr && ptrTiltMtr->state != MOTOR_IDLE) { ignoreCmd = true; Serial.println("Ignoring 'U'/'D': Tilt motor busy."); }
            break;
        case '1': // Lift Up
        case '3': // Lift Down
            if (ptrRightShoulderLiftMtr && ptrRightShoulderLiftMtr->state != MOTOR_IDLE) { ignoreCmd = true; Serial.println("Ignoring '1'/'3': Shoulder Lift motor busy."); }
            break;
        case '2': // Rot More
        case '4': // Rot Less
            if (ptrRightShoulderRotMtr && ptrRightShoulderRotMtr->state != MOTOR_IDLE) { ignoreCmd = true; Serial.println("Ignoring '2'/'4': Shoulder Rot motor busy."); }
            break;
        case '5':
        case '6':
        case '7':
        case '8':
            if (isMovingToPose) { ignoreCmd = true; Serial.println("Ignoring '5'-'8': MoveToPose busy."); }
            // Also check if individual shoulder motors are busy from single steps
            else if (ptrRightShoulderLiftMtr && ptrRightShoulderLiftMtr->state != MOTOR_IDLE) { ignoreCmd = true; Serial.println("Ignoring '5'-'8': Shoulder Lift motor busy."); }
            else if (ptrRightShoulderRotMtr && ptrRightShoulderRotMtr->state != MOTOR_IDLE) { ignoreCmd = true; Serial.println("Ignoring '5'-'8': Shoulder Rot motor busy."); }
            break;
        default:
            // Unknown commands are handled in parse()
            break;
    }

    // --- Interrupt Logic ---
    // If the command is NOT ignored AND moveToPose is active,
    // AND the command is one that affects the shoulder motors ('1' through '4'), interrupt moveToPose.
    if (!ignoreCmd && isMovingToPose && (cmdChar >= '1' && cmdChar <= '4')) {
       isMovingToPose = false;
       // Stop the shoulder motors immediately
       if(poseLiftMotorPtr && poseLiftMotorPtr->state == MOTOR_STEPPING_DC) {
           analogWrite(poseLiftMotorPtr->enPin, STOP);
           digitalWrite(poseLiftMotorPtr->in1Pin, LOW); digitalWrite(poseLiftMotorPtr->in2Pin, LOW);
           poseLiftMotorPtr->state = MOTOR_IDLE;
       }
       if(poseRotMotorPtr && poseRotMotorPtr->state == MOTOR_STEPPING_DC) {
           analogWrite(poseRotMotorPtr->enPin, STOP);
           digitalWrite(poseRotMotorPtr->in1Pin, LOW); digitalWrite(poseRotMotorPtr->in2Pin, LOW);
           poseRotMotorPtr->state = MOTOR_IDLE;
       }
       Serial.println("MoveToPose interrupted by new command.");
    }

    // --- Execute or Clear ---
    if (!ignoreCmd) {
        parse(); // Parse and initiate the new command if not ignored
    } else {
        // Clear the buffer because the command was ignored
       inputString[0] = '\0'; // Clear first char is enough for readCmdLine logic
       // Optional: Clear whole buffer for safety
       // for (int i = 0; i < bufLen; i++) { inputString[i] = '\0'; }
    }
  }
}

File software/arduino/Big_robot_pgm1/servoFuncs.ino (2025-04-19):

/*************************************************
 *
 * servo related funcs (Non-Blocking)
 *
 *************************************************/

// --- Configuration ---
const int WAVE_REPETITIONS = 2;
const int WAVE_STEP_DEGREES = 2;
const unsigned long WAVE_STEP_DELAY_MS = 15;
const int WAVE_MIN_POS = 0;
const int WAVE_MAX_POS = 180;
const int WAVE_RIGHT_PARK_POS = 93; // Neutral position for continuous servo

// --- Global State Variables (defined in .h, declared here) ---
WaveState waveLeftState = WAVE_IDLE;
unsigned long waveLeftNextStepMillis = 0;
int waveLeftCurrentPos = 0; // Start at min position
int waveLeftRepetitions = 0;

WaveState waveRightState = WAVE_IDLE;
unsigned long waveRightNextStepMillis = 0;
int waveRightCurrentPos = 0; // Start at min position
int waveRightRepetitions = 0;


// --- Left Wave (Standard Servo) ---

void startWaveLeft() {
  // Ignore command if already waving
  if (waveLeftState != WAVE_IDLE) {
    Serial.println("Left wave already in progress. Ignoring command.");
    return;
  }
  Serial.println("Starting Left Wave...");
  waveLeftRepetitions = WAVE_REPETITIONS;
  waveLeftCurrentPos = WAVE_MIN_POS; // Ensure starting position
  waveServo.write(waveLeftCurrentPos); // Go to start position
  waveLeftState = WAVE_UP; // Start by moving up
  waveLeftNextStepMillis = millis() + WAVE_STEP_DELAY_MS; // Schedule first step
}

void updateWaveLeft() {
  if (waveLeftState == WAVE_IDLE) {
    return; // Nothing to do
  }

  unsigned long currentTime = millis();
  if (currentTime >= waveLeftNextStepMillis) {
    // Time for the next step

    if (waveLeftState == WAVE_UP) {
      waveLeftCurrentPos += WAVE_STEP_DEGREES;
      if (waveLeftCurrentPos >= WAVE_MAX_POS) {
        waveLeftCurrentPos = WAVE_MAX_POS; // Clamp to max
        waveLeftState = WAVE_DOWN; // Change direction
      }
      waveServo.write(waveLeftCurrentPos);
      waveLeftNextStepMillis = currentTime + WAVE_STEP_DELAY_MS; // Schedule next step
    }
    else if (waveLeftState == WAVE_DOWN) {
      waveLeftCurrentPos -= WAVE_STEP_DEGREES;
      if (waveLeftCurrentPos <= WAVE_MIN_POS) {
        waveLeftCurrentPos = WAVE_MIN_POS; // Clamp to min
        waveLeftRepetitions--; // Completed one full cycle (up and down)
        if (waveLeftRepetitions <= 0) {
          waveLeftState = WAVE_IDLE; // Finished all repetitions
          Serial.println("Left Wave Complete.");
          // No need to park standard servo, it holds position
          return; // Exit early, no more steps scheduled
        } else {
          waveLeftState = WAVE_UP; // Start next repetition
        }
      }
      waveServo.write(waveLeftCurrentPos);
      waveLeftNextStepMillis = currentTime + WAVE_STEP_DELAY_MS; // Schedule next step
    }
  }
}


// --- Right Wave (Continuous Rotation Servo) ---

void startWaveRight() {
  // Ignore command if already waving
  if (waveRightState != WAVE_IDLE) {
     Serial.println("Right wave already in progress. Ignoring command.");
    return;
  }
  Serial.println("Starting Right Wave...");
  waveRightRepetitions = WAVE_REPETITIONS;
  waveRightCurrentPos = WAVE_MIN_POS; // Start at one end of the "sweep"
  waveServo_right.write(waveRightCurrentPos); // Go to start position
  waveRightState = WAVE_UP; // Start by moving "up" (increasing position value)
  waveRightNextStepMillis = millis() + WAVE_STEP_DELAY_MS; // Schedule first step
}

void updateWaveRight() {
  if (waveRightState == WAVE_IDLE) {
    return; // Nothing to do
  }

  unsigned long currentTime = millis();
  if (currentTime >= waveRightNextStepMillis) {
    // Time for the next step

    if (waveRightState == WAVE_UP) {
      waveRightCurrentPos += WAVE_STEP_DEGREES;
      if (waveRightCurrentPos >= WAVE_MAX_POS) {
        waveRightCurrentPos = WAVE_MAX_POS; // Clamp to max
        waveRightState = WAVE_DOWN; // Change direction
      }
      waveServo_right.write(waveRightCurrentPos);
      waveRightNextStepMillis = currentTime + WAVE_STEP_DELAY_MS; // Schedule next step
    }
    else if (waveRightState == WAVE_DOWN) {
      waveRightCurrentPos -= WAVE_STEP_DEGREES;
      if (waveRightCurrentPos <= WAVE_MIN_POS) {
        waveRightCurrentPos = WAVE_MIN_POS; // Clamp to min
        waveRightRepetitions--; // Completed one full cycle (up and down)
        if (waveRightRepetitions <= 0) {
          waveServo_right.write(WAVE_RIGHT_PARK_POS); // Park the continuous servo
          waveRightState = WAVE_IDLE; // Finished all repetitions
          Serial.println("Right Wave Complete.");
          return; // Exit early, no more steps scheduled
        } else {
          waveRightState = WAVE_UP; // Start next repetition
        }
      }
      waveServo_right.write(waveRightCurrentPos);
      waveRightNextStepMillis = currentTime + WAVE_STEP_DELAY_MS; // Schedule next step
    }
  }
}

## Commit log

2025-03-03 initial arduino code commit
2025-03-22 added motor movements
2025-04-05 Add right wrist servo, fix feedback pot
    [Big_robot_pgm1.ino, Parser.ino, initializationFuncs.ino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]
2025-04-18 document motors & API
2025-04-19 Add camera listing prog
2025-04-19 refactor: Implement non-blocking motor control and command handling
2025-04-19 fix: Resolve motor type errors and remove obsolete functions
2025-04-19 feat: Refine moveToPose interrupt logic for motor commands
2025-04-19 refactor: Remove unnecessary forward declaration of motor struct
2025-04-25 added serial read buffer clear add hand arm movements when face detected
2025-04-25 Added head positioning at startup changed loop delay of 0.5 sec to stabilize camera view Added sanning for face when one is not detected fixed periodic arm/wrist motion when a face is detected at cen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
    [facedet_test.py]
